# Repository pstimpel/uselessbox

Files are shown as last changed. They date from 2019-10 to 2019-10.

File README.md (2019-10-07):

# uselessbox
Just another useless box

3D printed useless box or so called useless machines. Arduino driven. Features 4 servos and a gesture/proximity sensor. Contains a 16 LED neopixel ring. All parts are easy to source. 

## Video in Action
https://www.youtube.com/watch?v=pDcApzEbbxg

## List of parts, sources (no affiliate links)
1x Arduino Nano V3 5V

1x Gesture/proximity sensor, 5V (!) similar to https://www.distrelec.de/de/naeherungs-licht-rgb-und-gestensensor-apds9960-5v-adafruit-3595/p/30139163

1x switch, similar to https://www.amazon.de/gp/product/B07MY2WVQ3/

1x jack similar to https://www.amazon.de/gp/product/B009PH1J5Y/

1x power adaptor similar to https://www.amazon.de/gp/product/B07HSPT57Y

4x servo motors, similar to https://www.amazon.de/gp/product/B06XQD18QN

cables, solder stuff

22x M3*10 scews

5x M3*8 screws

2x M3*20 screws

1x Neopixel 16 LED ring similar to https://www.distrelec.de/de/neopixel-ring-mit-16-rgb-leds-adafruit-1463-neopixel/p/30091142

1x resistor 1/4W 260 Ohm

1x resistor 1/4W 10 kOhm

20x 2.54mm pin headers

2x 5mm 2pol screw terminals

some steering servo push wire, 0.6mm will do. You need about 10 cm.

some double sided tape

optional: stuff to create PCBs

## Instructions
Optional: create your PCB

Just 3d print the parts, each part one time. I printed the "OK fingers" in 0.1mm, and all other stuff in 0.25mm. I used cubic infill, 2 shells, and 3 shells on bottom and top. I did not use any support except for the LED housing. I was using PLA from https://dasfilament.de

Mount one servo to the back part. The axis on top is showing to the outside. Add the lid servo arm. Mount the lid to the back using M3*20 screws. Now use the steering servo push wire. Make sure your servo is at center position when doing that. Make the wire as long as you need it so the lid and back are located rectangular.

Mount the back to the bottom, using 4 M3*10 screws. 

Mount the usb door using the usb door frame, to the the front. Mount the front to the bottom using 4 M3*10 screws.

Mount the jack to the bottom rear and lock it using the "Buchsenhalter" (sorry, forgot to translate it) to the bottom. Use 2 M3*8 screws.

Solder 5 cables to the gesture sensor board, but do not use the pins for this breakout board. If you have, use some old servo cable or anything similar that would match to pins at your main board if you use any. If there are no pins, you will have to solder the wires to the main board later. Make the cables around 15cm long. Mount the sensor board to the top, using the Sensorlock and 2 M3*8 screws.

Solder 2 cables to your switch. Mount the switch to the top. The "on position" of the switch has to show away from the sensor board. Make these cables around 15cm long.

Solder 3 more cables to your neopixel ring (ground, V+, data in). Make these cables 15 cm long, and use again some old servo cables or other cables matching pins. Add the neopixel ring to the housing, and close it using the LED cover. Btw, print this in transparent filament, if you have. Nice light effects are waiting for you. Lock the housing and the cover by another M3*8 screw. The neopixel ring points towards the cover with its LEDs. Mount the LED housing on top of your top part, and lock it using some M3*10 screws. The LED point towards the front. Moint the "flag arm" to one servo, and this servo to the top part. If you look from behind, the axis points to you and to the left. You can add some white label to the flag holder, to create a small flag. Mount the top to the front using another 4 M3*10 screws.

Mount the finger to one servo, do not lock it up yet. Mount the servo to the right housing part, axis to the right. Mount the right housing to the already mounted parts, mount it on the right side when you look from behind! Use 5 M3*10 screws.

OK, we enter the finish line, slowly...

Mount the 4th servo to the "left" part. Axis point to the front, but downwards. Connect OK fingers and "assholearm" together using another M3*10 screw. Mount the whole arm to the servo. DO NOT CLOSE THE HOUSING YET!

Connect all wires (servos, LED, switch, jack, gesture sensor) to your PCB. Take care for not short cutting anything. Use double sided tape and mount your PCB in a way you can reach the USB of te arduino throught the "usb door" at the front of your housing. Make sure again you do not block any servo movement by cables.

It is time to connect the power adaptor. If nothing smokes, you got your solder job the right way.

Make sure the switch on top of your new toy is in Off position, pointing to the front. Connect USB and your PC. Fire up your Arduino IDE, load the sketch and push it to the Arduino. Maybe you need to activate libraries for servos, or FastLED or the gesture sensor. Just follow the instruction of these vendors.

After the reboot, the LED should light up in blue and kind of glow...if you put your finger on the sensor, it should glow red, brightness depending on how close your finger is to the sensor.

At the same time, all your servos were "reset". You can now tighten all the screws of the servo arms connecting to the servo heads.

Servo for Lid: in reset position the LID should be closed

Servo for Flag: in reset position the flag arm should be horizontal, but below the edge of the top.

Servo for OKFinger/Asshole: The door should be closed, the fingers hidden.

Servo for Finger: Tricky one. Push the switch backwards and watch your finger if it makes it way to the switch. Idealy, it should turn the switch off. Just adjust until this happens. Hint: give a little extra push, just about 2-3 mm. Finally, tighten the screw.

OK, if all mechanics are working as expected, your useless machine should work as expected. You can now close the housing, using the last 5 M3*10 screws.

## What does it do?
Basically, the Arduino will cycle trough different ways the servos work. To start the machine, just push the switch to on. The main task of this machine is to push the switch into its off position.

Step 1: open lid, push switch off

Step 2: open lid very harsh, push switch off. After that the lid will open depending on how close your finger is to the sensor.

Step 3: open lid again, push switch off

Step 4: open lid, waving white flag, close the lid. Open the lid, push off the switch, close the lid.

Step 5: show the OK finger / asshole finger (as you prefer), then open the lid, push the switch, close the lid.

Of course you are invited to extent the possible action, color codes and so on. Just make sure to not use "delay()" too heavy, since this will interrupt the glowing of the LED.

## Frequently asked questions
### Why do you enable and disable the servos that much?
I found my servos to be really cheap ones. They interfere with each other. Disabling the servos I do not need for the moment solved this. However, in the video you can see the servos "choking". If you can, buy quality servos.

## Credits
The "OK finger" was remixed out of https://www.thingiverse.com/thing:3370059 by tdkahn1978 .

## Crosslinks

Repo
https://github.com/pstimpel/uselessbox

Thingiverse
https://www.thingiverse.com/thing:3901482

Prusaprinters
https://www.prusaprinters.org/prints/6042-another-useless-box

Youtube
https://www.youtube.com/watch?v=pDcApzEbbxg

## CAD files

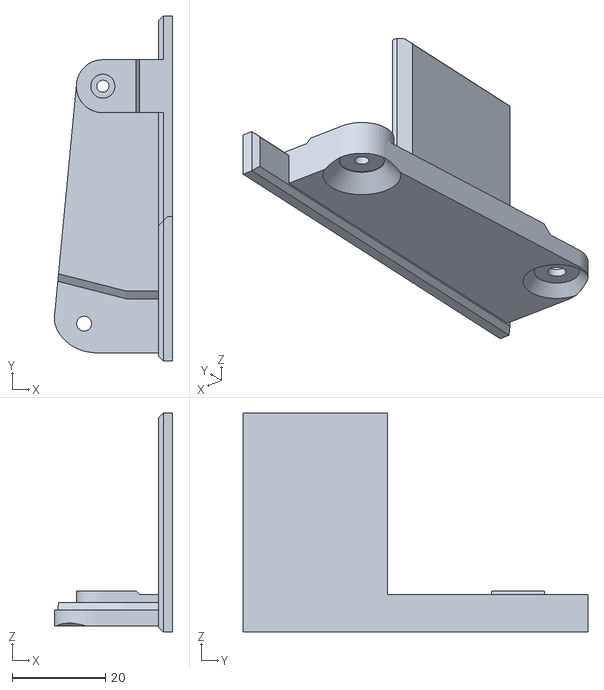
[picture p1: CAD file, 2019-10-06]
stl/AssholeArmv5.stl
25.4 x 74.0 x 47.0

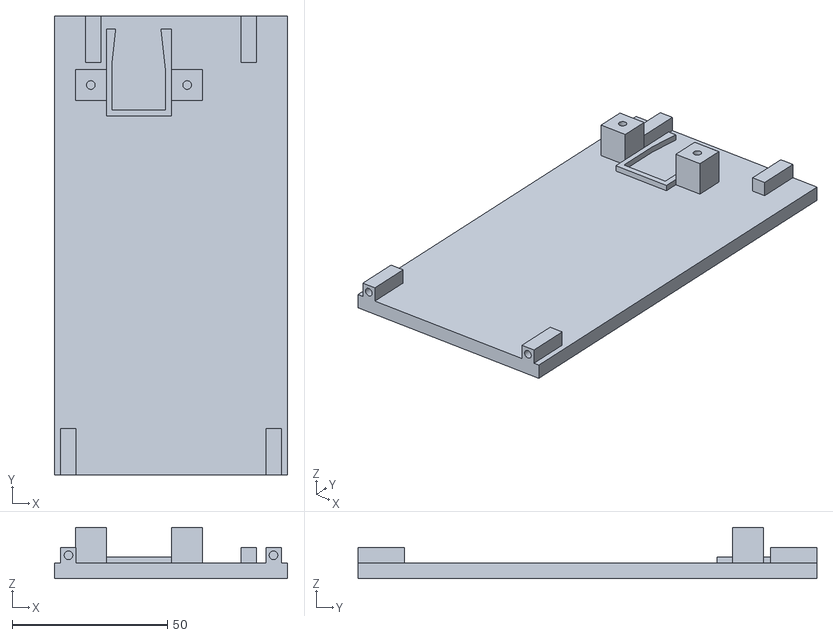
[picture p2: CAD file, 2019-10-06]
stl/BottomV2.stl
75.0 x 147.7 x 16.5

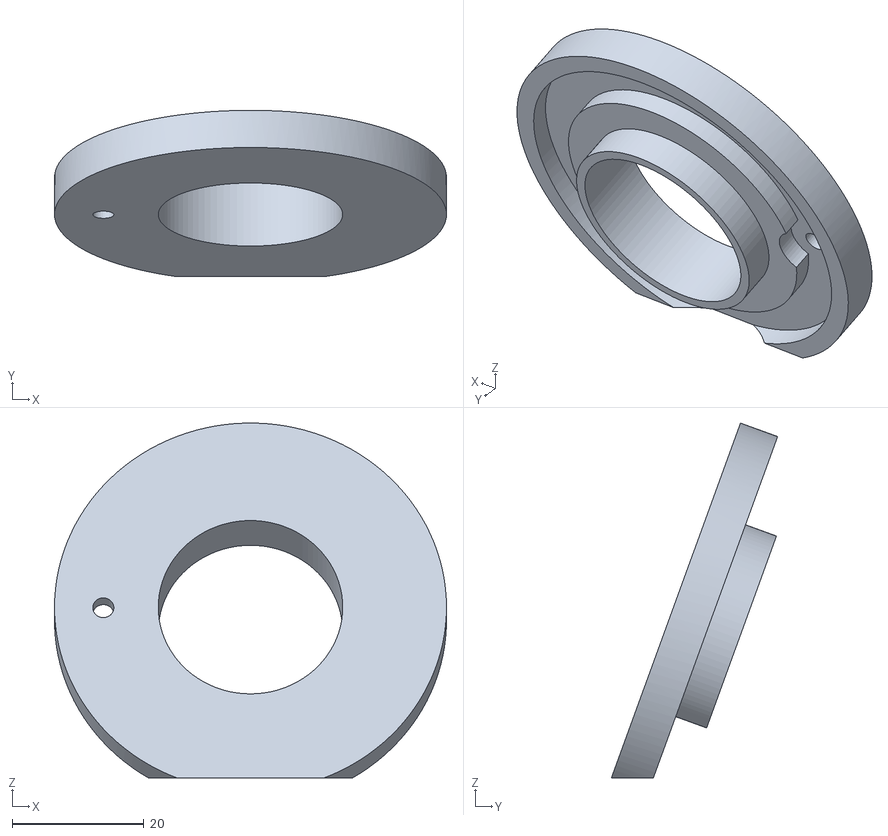
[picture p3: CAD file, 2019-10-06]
stl/LEDCoverv4.stl
59.5 x 25.2 x 53.9

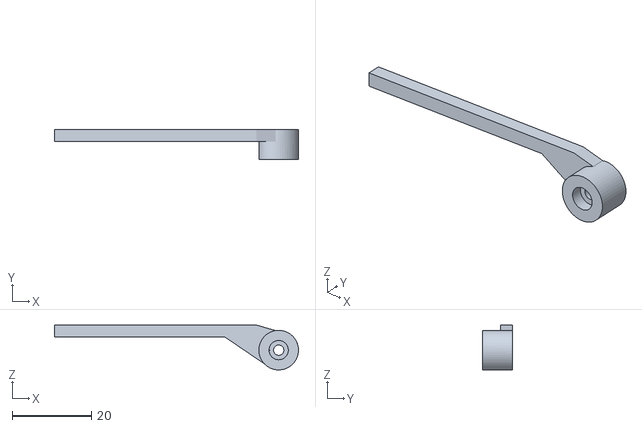
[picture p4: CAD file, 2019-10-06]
stl/WhiteFlagv5.stl
61.6 x 7.50 x 11.3

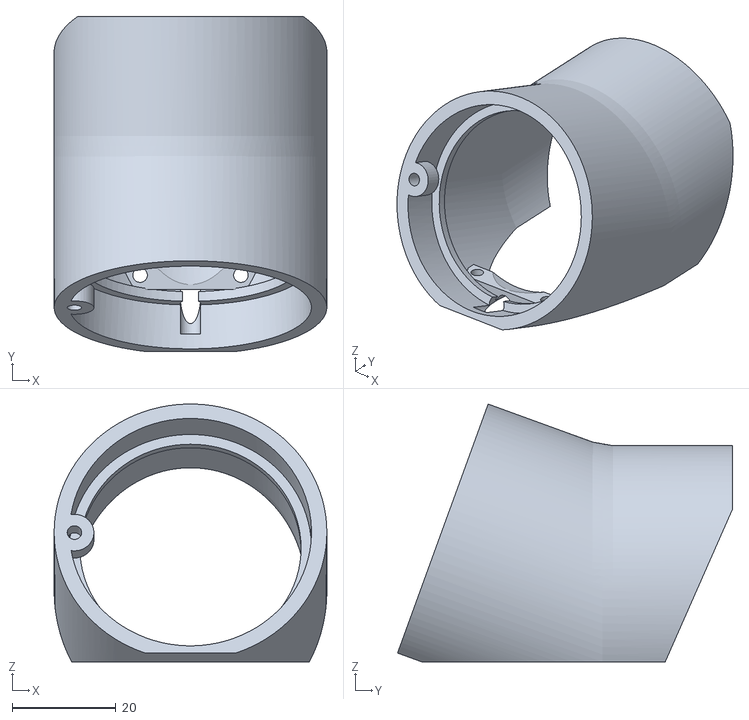
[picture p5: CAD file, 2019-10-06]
stl/LEDhousingv10.stl
52.5 x 64.5 x 49.6

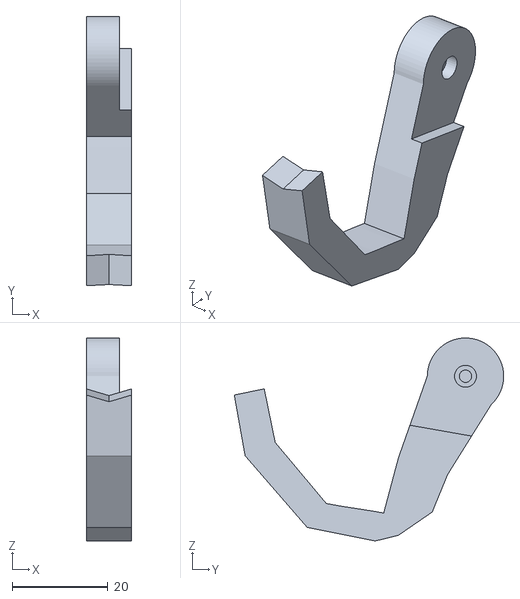
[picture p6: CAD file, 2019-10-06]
stl/Fingerv8.stl
9.50 x 56.4 x 42.5

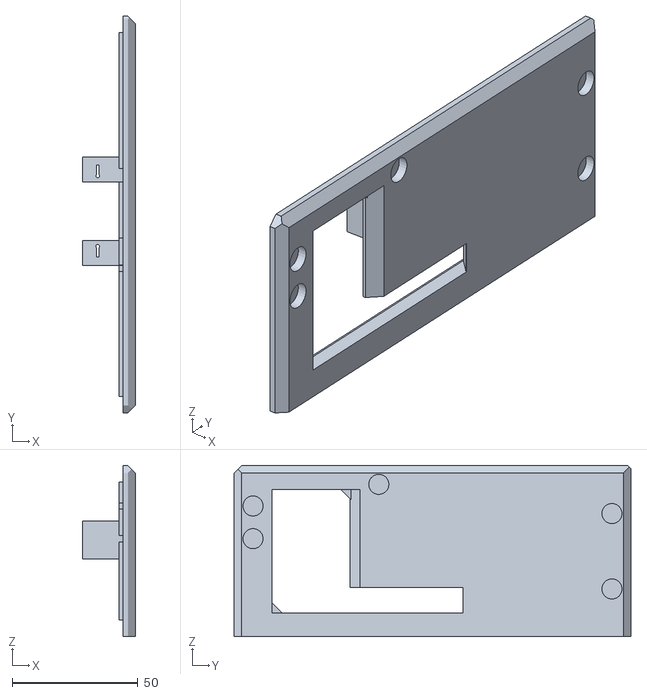
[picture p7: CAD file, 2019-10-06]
stl/Leftv5.stl
21.0 x 157.7 x 68.0

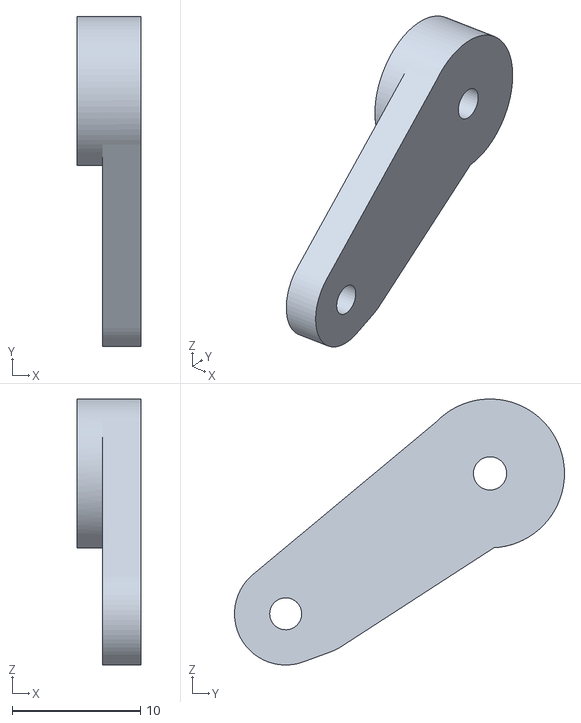
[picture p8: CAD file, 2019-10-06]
stl/LidServoArmv4.stl
5.00 x 25.8 x 20.8

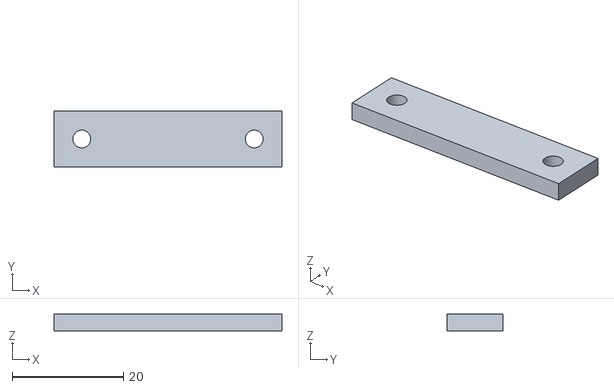
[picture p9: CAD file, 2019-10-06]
stl/BuchsenhalterV2.stl
41.0 x 10.0 x 3.00

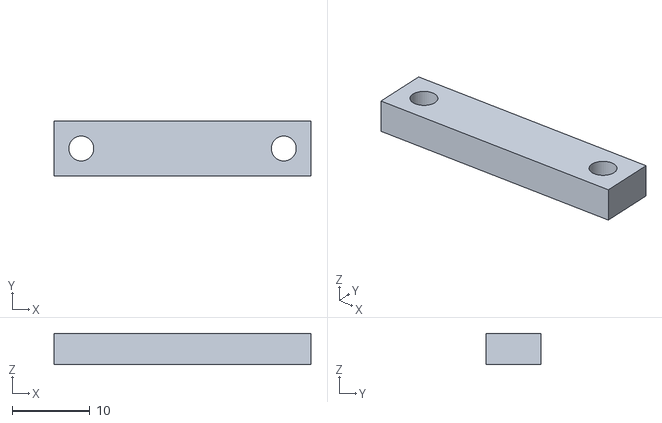
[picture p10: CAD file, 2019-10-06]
stl/SensorLockV2.stl
33.0 x 7.00 x 4.00

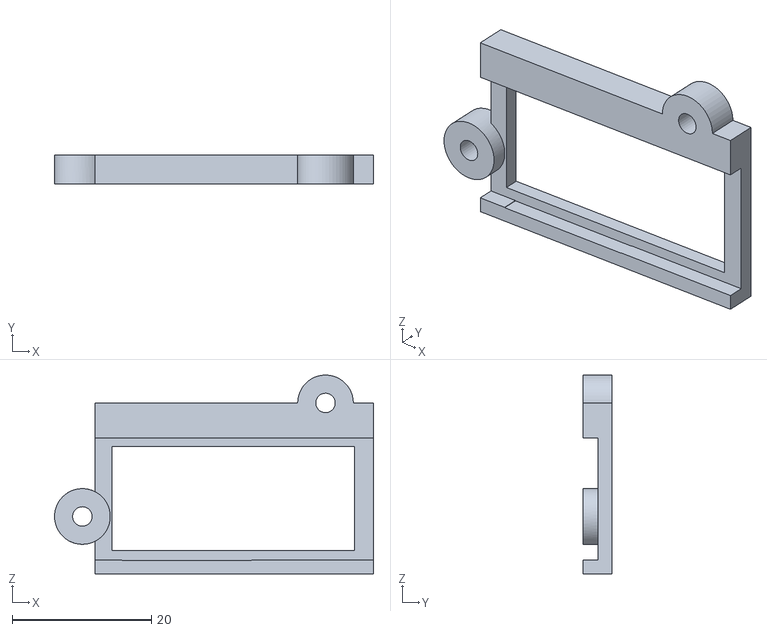
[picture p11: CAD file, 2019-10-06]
stl/USBDoorFrameV2.stl
45.8 x 4.20 x 28.6

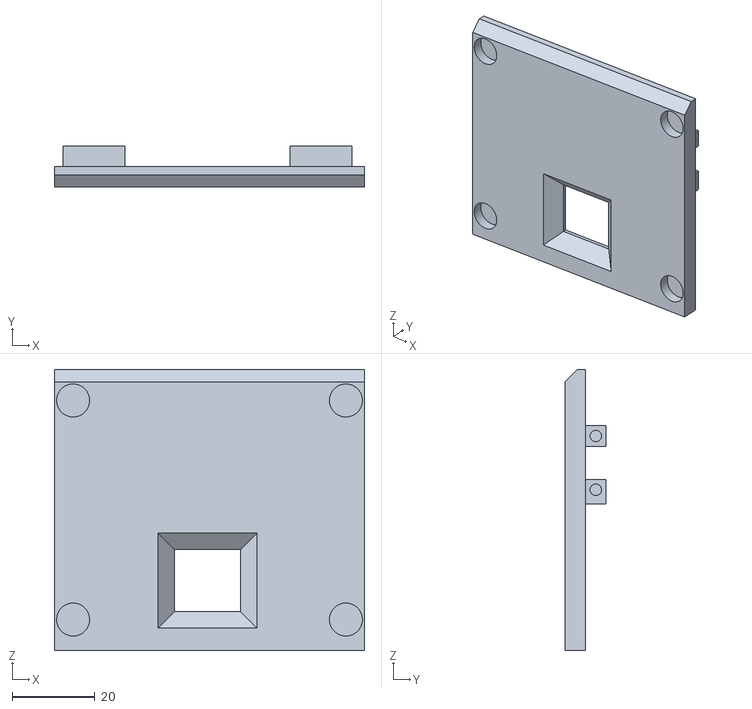
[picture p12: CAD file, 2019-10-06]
stl/FrontV2.stl
75.0 x 10.0 x 68.0

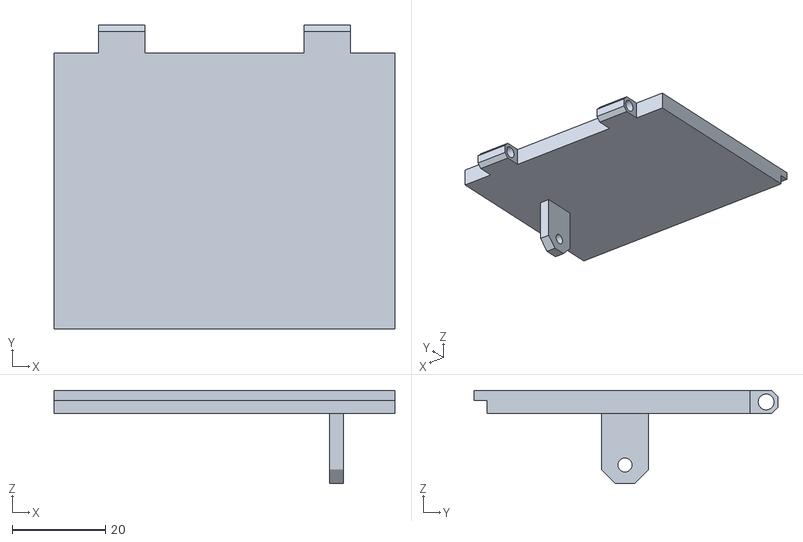
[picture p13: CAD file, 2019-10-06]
stl/LidV2.stl
73.0 x 65.0 x 20.0

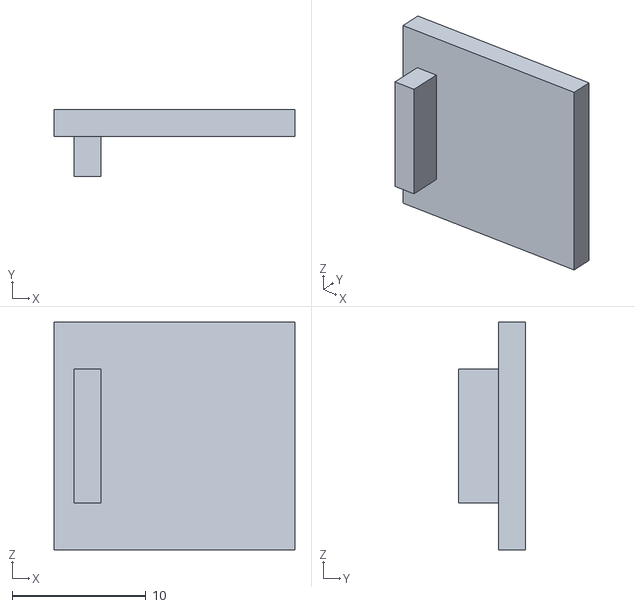
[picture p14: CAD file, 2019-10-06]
stl/USBDoorV2.stl
18.0 x 5.00 x 17.0

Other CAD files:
stl/Backv4.stl
stl/Topv5.stl
stl/RightV4.stl
stl/OKFinger v2.stl

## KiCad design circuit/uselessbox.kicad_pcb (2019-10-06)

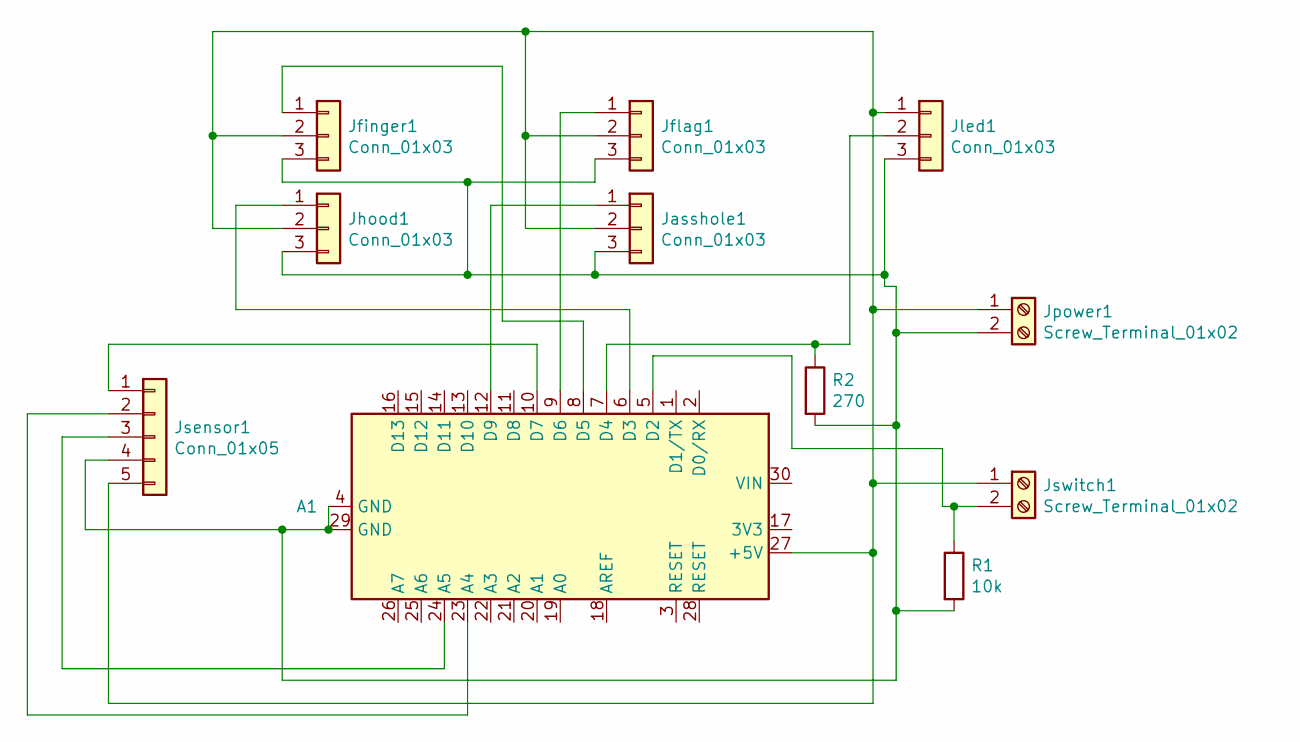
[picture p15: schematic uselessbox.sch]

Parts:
A1: n; Arduino_Nano
Jasshole1: Conn_01x03; PinHeader_1x03_P2.54mm_Vertical
Jfinger1: Conn_01x03; PinHeader_1x03_P2.54mm_Vertical
Jflag1: Conn_01x03; PinHeader_1x03_P2.54mm_Vertical
Jhood1: Conn_01x03; PinHeader_1x03_P2.54mm_Vertical
Jled1: Conn_01x03; PinHeader_1x03_P2.54mm_Vertical
Jpower1: Screw_Terminal_01x02; TerminalBlock_Altech_AK300-2_P5.00mm
Jsensor1: Conn_01x05; PinHeader_1x05_P2.54mm_Vertical
Jswitch1: Screw_Terminal_01x02; TerminalBlock_Altech_AK300-2_P5.00mm
R1: 10k; R_Axial_DIN0204_L3.6mm_D1.6mm_P7.62mm_Horizontal
R2: 270; R_Axial_DIN0204_L3.6mm_D1.6mm_P7.62mm_Horizontal

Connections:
unnamed: A1.5 (D2), Jswitch1.2, R1.1
unnamed: A1.6 (D3), Jhood1.1
unnamed: A1.7 (D4), Jled1.2, R2.1
unnamed: A1.8 (D5), Jfinger1.1
unnamed: A1.9 (D6), Jflag1.1
unnamed: A1.10 (D7), Jsensor1.1
unnamed: A1.12 (D9), Jasshole1.1
unnamed: A1.23 (A4), Jsensor1.2
unnamed: A1.24 (A5), Jsensor1.3
unnamed: A1.27 (+5V), Jasshole1.2, Jfinger1.2, Jflag1.2, Jhood1.2, Jled1.1, Jpower1.1, Jsensor1.5, Jswitch1.1
unnamed: A1.4 (GND), A1.29 (GND), Jasshole1.3, Jfinger1.3, Jflag1.3, Jhood1.3, Jled1.3, Jpower1.2, Jsensor1.4, R1.2, R2.2

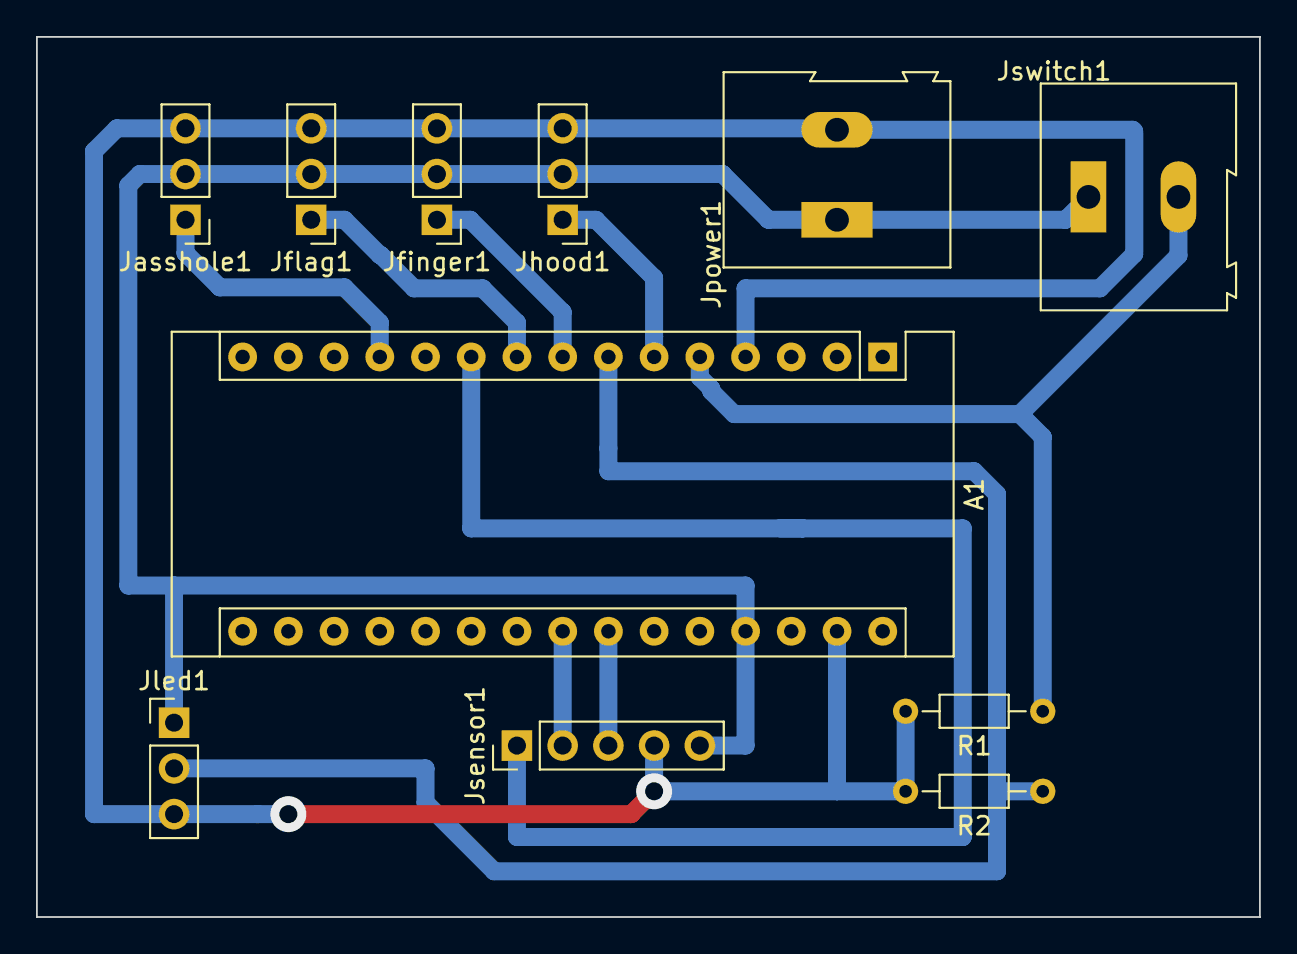
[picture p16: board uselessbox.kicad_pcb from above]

Board: 2 copper layers, 67.9 x 48.9 mm, 11 parts (0 on the bottom side), 11 nets.

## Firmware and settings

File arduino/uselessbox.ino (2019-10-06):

#include <FastLED.h>
#include <Servo.h>
#include "Adafruit_APDS9960.h"
Adafruit_APDS9960 apds;


FASTLED_USING_NAMESPACE

Servo hood, finger, flag, asshole;

#if defined(FASTLED_VERSION) && (FASTLED_VERSION < 3001000)
#warning "Requires FastLED 3.1 or later; check github for latest code."
#endif

#define INT_PIN 7

#define DATA_PIN    4
//#define CLK_PIN   4
#define LED_TYPE    WS2811
#define COLOR_ORDER GRB
#define NUM_LEDS    16
CRGB leds[NUM_LEDS];
CRGBPalette16 gPal;
volatile bool glowstate = false;
volatile int brightness = 150;
volatile int colorcode =1;
int presetbrightness = 150;

int hoodactivestop = 1000;
int hoodinactivestop = 1650;
volatile int hoodcurrent = 1650;
volatile int hoodspeed = 25;
volatile bool hoodservoactive = false;

int fingeractivestop = 1700;
int fingerinactivestop = 1300;
volatile int fingercurrent = 1300;
volatile int fingerspeed = 250;
volatile bool fingerservoactive = false;

int flagactivestop = 2000;
int flaginactivestop = 1500;
volatile int flagcurrent = 1500;
volatile int flagspeed = 150;
volatile bool flagservoactive = false;

int assholeactivestop = 1000;
int assholeinactivestop = 1700;
volatile int assholecurrent = 1700;
volatile int assholespeed = 50;
volatile bool assholeservoactive = false;

volatile bool servoactive = false;
volatile bool servoactionfinished = false;

volatile int currentstep=0;
volatile bool currentstepfinished=false;

volatile bool skipflag = false;
volatile bool skipasshole = false;

#define FRAMES_PER_SECOND  120

volatile bool triggerInUse=false;
volatile bool triggerinprogress = false;

volatile int localloop =-1;

int lowerproximitythreshold=15;

int servopinhood = 3;
int servopinfinger = 5;
int servopinflag = 6;
int servopinasshole = 9;

int pinswitch = 2;
volatile int oldhoodcurrent=0;

void setup() {
  Serial.begin(9600); //init debug console 
  pinMode(INT_PIN, INPUT_PULLUP);
  delay(500); // 500 milliseconds delay for recovery
  pinMode(3, INPUT); //modeswitch
  FastLED.addLeds<LED_TYPE,DATA_PIN,COLOR_ORDER>(leds, NUM_LEDS).setCorrection(TypicalLEDStrip);
  FastLED.setBrightness(brightness);
  if(!apds.begin()){
    Serial.println("failed to initialize device! Please check your wiring.");
  }
  else Serial.println("Device initialized!");

  apds.enableProximity(true);
  apds.setProximityInterruptThreshold(0, lowerproximitythreshold);
  apds.enableProximityInterrupt();
  
  setled(CRGB::White);
  //delay(5000);
  hoodcurrent = hoodinactivestop;
  movehood(hoodcurrent);
  fingercurrent = fingerinactivestop;
  movefinger(fingercurrent);
  flagcurrent = flaginactivestop;
  moveflag(flagcurrent);
  assholecurrent = assholeinactivestop;
  moveasshole(assholecurrent);
  
  enableServos();
  delay(500);  
  servoactive = true;
  executeServo();
  delay(500);
  disableServos();
  delay(500);
  servoactive = false;
  servoactionfinished = true;
  
  setled(CRGB::Black);
  brightness=10;
  
}



void loop()
{

  
  if(!digitalRead(INT_PIN)){
    setled(CRGB::DarkRed);
    int proximity = apds.readProximity();
    //Serial.println(proximity);
    FastLED.setBrightness(proximity);
    //clear the interrupt
    apds.clearInterrupt();
    if(localloop==1) {
      if(hoodservoactive==false) {
        enableServoHood();
        delay(100);
        oldhoodcurrent = hoodcurrent;
      }
      hoodcurrent = map(proximity, lowerproximitythreshold, 255, hoodinactivestop, hoodactivestop);
      if(hoodcurrent > (oldhoodcurrent + 50) || hoodcurrent < (oldhoodcurrent - 50)) {
        oldhoodcurrent=hoodcurrent;
        movehood(hoodcurrent);
        //Serial.println(hoodcurrent);
      }
      if(hoodservoactive==true) {
        disableServoHood();
      }
    }
    
  } else {
    
    FastLED.setBrightness(brightness);
    glow();
  }
  FastLED.show();  
  FastLED.delay(1000/FRAMES_PER_SECOND); 
  
  if(digitalRead(pinswitch) == HIGH) {
    if(triggerInUse==false && triggerinprogress==false) {  
      triggerinprogress=true;
      brightness=presetbrightness;
      FastLED.setBrightness(brightness);
      //Serial.println("------------>trigger");  
      localloop++;
      if (localloop > 5) {
        localloop = 0;
      }
      switch (localloop) {
        case 0: //standard
          skipflag = true;
          skipasshole = true;
          hoodspeed = 25;
          fingerspeed = 250;
          flagspeed = 50;
          assholespeed = 50;
          colorcode=2;
        break;
        case 1: //fast and resolute
          skipflag = true;
          skipasshole = true;
          hoodspeed = 200;
          fingerspeed = 250;
          flagspeed = 250;
          assholespeed = 50;
          colorcode=5;
        break;
        case 2: //open hood based on proximity
          skipflag = true;
          skipasshole = true;
          hoodspeed = 25;
          fingerspeed = 250;
          flagspeed = 150;
          assholespeed = 50;
          colorcode=3;
        break;
        case 3: //wave flag
          skipflag = false;
          skipasshole = true;
          hoodspeed = 25;
          fingerspeed = 250;
          flagspeed = 150;
          assholespeed = 50;
          colorcode=3;
        break;
        case 4: //really slow
          skipflag = true;
          skipasshole = true;
          hoodspeed = 10;
          fingerspeed = 250;
          flagspeed = 150;
          assholespeed = 50;
          colorcode=2;
        break;
        case 5: //show asshole
          skipflag = true;
          skipasshole = false;
          hoodspeed = 25;
          fingerspeed = 250;
          flagspeed = 150;
          assholespeed = 50;
          colorcode=4;
        break;
        default:
          skipflag = true;
          skipasshole = true;
          hoodspeed = 25;
          fingerspeed = 250;
          flagspeed = 150;
          assholespeed = 50;
          colorcode=2;
        break;
      }
      //Serial.print("loop:");
      //Serial.println(localloop);
      servoactive=true;
      servoactionfinished=false;
      currentstep=1;
      currentstepfinished=false;

      //enableServos();

      setled(CRGB::White);
      FastLED.show();
      delay(250);
      

      
      
    } else {
      //Serial.println("----------Trigger in use already");
    }
      
  } else {
    if(triggerInUse==true) {
      brightness=presetbrightness;
      FastLED.setBrightness(brightness);
      //Serial.println("------------>trigger release");  
      setled(CRGB::Black);
      triggerInUse=false;
      triggerinprogress=false;
    }
  }
  
  if(servoactionfinished==true) {
    colorcode=1;
    if(servoactive==true) {
      //disableServos();
      servoactive=false;
      currentstep=0;
    }
    servoactive = false;
    triggerInUse=false;
    triggerinprogress=false;
    
  }
  
  if(servoactive==true && servoactionfinished==false) {

    
    
    //do math staff and so on
    if(currentstepfinished==true && currentstep==9) {
      servoactionfinished=true;
      if(hoodservoactive==true) {
        disableServoHood();
      }
    }
    
    if(currentstepfinished==false && currentstep==8) {
      if(fingerservoactive==true) {
        disableServoFinger();
      }
      if(hoodservoactive==false) {
        enableServoHood();
      }
      if(hoodcurrent < hoodinactivestop) {
        if(hoodcurrent <= (hoodinactivestop - hoodspeed)) {
          hoodcurrent=hoodcurrent+(hoodspeed-1);
          //Serial.println("close hood");
        } else {
          hoodcurrent=hoodinactivestop;
          currentstepfinished=true;
          currentstep++;
          //Serial.println("closed hood");
        }
      }
    }

    if(currentstepfinished==false && currentstep==7) {
      if(fingercurrent > fingerinactivestop) {
        if(fingercurrent >= (fingerinactivestop + fingerspeed)) {
          fingercurrent=fingercurrent-(fingerspeed-1);
          //Serial.println("close finger");
        } else {
          fingercurrent=fingerinactivestop;
          currentstepfinished=false;
          currentstep++;
          //Serial.println("closed finger");
        }
      }
    }

    if(currentstepfinished==false && currentstep==6) {
      if(fingerservoactive==false) {
        enableServoFinger();
      }
      if(flagservoactive==true) {
        disableServoFlag();
      }
      if(fingercurrent < fingeractivestop) {
        if(fingercurrent <= (fingeractivestop - fingerspeed)) {
          fingercurrent=fingercurrent+(fingerspeed-1);
          //Serial.println("raise finger");
        } else {
          fingercurrent=fingeractivestop;
          currentstepfinished=false;
          currentstep++;
          //Serial.println("stay finger");
        }
      }
    }

        
    if(currentstepfinished==false && currentstep==5) {
      
      if(skipflag == true) {
        currentstep++;
      } else {
        if(flagcurrent > flaginactivestop) {
          if(flagcurrent >= (flaginactivestop + flagspeed)) {
            flagcurrent=flagcurrent-(flagspeed-1);
            //Serial.println("close flag");
          } else {
            flagcurrent=flaginactivestop;
            currentstepfinished=false;
            currentstep++;
            //Serial.println("closed flag");
          }
        }
        
      }
    }
    
    if(currentstepfinished==false && currentstep==4) {
      if(hoodservoactive==true) {
        disableServoHood();
      }
      if(skipflag == true) {
        currentstep++;
      } else {
        if(flagservoactive==false) {
          enableServoFlag();
        }
        if(flagcurrent < flagactivestop) {
          if(flagcurrent <= (flagactivestop - flagspeed)) {
            flagcurrent=flagcurrent+(flagspeed - 1);
            //Serial.println("raise flag");
          } else {
            flagcurrent=flagactivestop;
            currentstepfinished=false;
            currentstep++;
            //Serial.println("stay flag");
            //waving the flag
            moveflag(flagcurrent);
            delay(200);
            flagcurrent = flagcurrent-50;
            moveflag(flagcurrent);
            delay(200);
            flagcurrent = flagcurrent-50;
            moveflag(flagcurrent);
            delay(200);
            flagcurrent = flagcurrent+50;
            moveflag(flagcurrent);
            delay(200);
            flagcurrent = flagcurrent+50;
            moveflag(flagcurrent);
            delay(200);
            flagcurrent = flagcurrent-50;
            moveflag(flagcurrent);
            delay(200);
            flagcurrent = flagcurrent-50;
            moveflag(flagcurrent);
            delay(200);
            flagcurrent = flagcurrent+50;
            moveflag(flagcurrent);
            delay(200);
            flagcurrent = flagcurrent+50;
            moveflag(flagcurrent);
            delay(200);
            flagcurrent = flagactivestop;
            
          }
        }
      }
    }
  
    if(currentstepfinished==false && currentstep==3) {
      if(assholeservoactive==true) {
        disableServoAsshole();
      }
      if(hoodservoactive==false) {
        enableServoHood();
      }
      if(hoodcurrent > hoodactivestop) {
        if(hoodcurrent >= (hoodactivestop + hoodspeed)) {
          hoodcurrent=hoodcurrent-(hoodspeed - 1);
          //Serial.println("raise hood");
        } else {
          hoodcurrent=hoodactivestop;
          currentstepfinished=false;
          currentstep++;
          //Serial.println("stay hood");
        }
      }
    }

    if(currentstepfinished==false && currentstep==2) {
      
      if(skipasshole == true) {
        currentstep++;
      } else {
        if(assholecurrent < assholeinactivestop) {
          if(assholecurrent <= (assholeinactivestop - assholespeed)) {
            assholecurrent=assholecurrent+(assholespeed-1);
            //Serial.println("close asshole");
          } else {
            assholecurrent=assholeinactivestop;
            currentstepfinished=false;
            currentstep++;
            //Serial.println("closed asshole");
          }
        }
        
      }
    }
    
    if(currentstepfinished==false && currentstep==1) {
     
      if(skipasshole == true) {
        currentstep++;
      } else {
        if(assholeservoactive==false) {
          enableServoAsshole();
        }
        if(assholecurrent > assholeactivestop) {
          if(assholecurrent >= (assholeactivestop + assholespeed)) {
            assholecurrent=assholecurrent-(assholespeed - 1);
            //Serial.println("raise asshole");
          } else {
            assholecurrent=assholeactivestop;
            currentstepfinished=false;
            currentstep++;
            //Serial.println("stay asshole");
            delay(2000);
          }
        }
      }
    }
  

    
    executeServo();
    delay(50);
  }
  
}

void enableServoHood() {
  hood.attach(servopinhood);
  hoodservoactive=true;
}
void enableServoFinger() {
  finger.attach(servopinfinger);
  fingerservoactive=true;
}
void enableServoFlag() {
  flag.attach(servopinflag);
  flagservoactive=true;
}
void enableServoAsshole() {
  asshole.attach(servopinasshole);
  assholeservoactive=true;
}
void disableServoHood() {
  hood.detach();
  hoodservoactive=false;
}
void disableServoFinger() {
  finger.detach();
  fingerservoactive=false;
}
void disableServoFlag() {
  flag.detach();
  flagservoactive=false;
}
void disableServoAsshole() {
  asshole.detach();
  assholeservoactive=false;
}

void enableServos() {
  hood.attach(servopinhood);
  finger.attach(servopinfinger);
  flag.attach(servopinflag);
  asshole.attach(servopinasshole);
  //delay(500);
}

void disableServos() {
  hood.detach();
  finger.detach();
  flag.detach();
  asshole.detach();
  //delay(500);
}

void executeServo() {
  if(servoactive==true) {
    //hood
    movehood(hoodcurrent);
    //Serial.print("hood Servo moved to ");
    //Serial.println(hoodcurrent);
    
    //finger
    movefinger(fingercurrent);
    //Serial.print("finger Servo moved to ");
    //Serial.println(fingercurrent);
    
    //flag
    moveflag(flagcurrent);
    //Serial.print("flag Servo moved to ");
    //Serial.println(flagcurrent);
    
    //asshole
    moveasshole(assholecurrent);
    //Serial.print("asshole Servo moved to ");
    //Serial.println(assholecurrent);
    
  }
}




void movefinger(int speed) {
  int angle = map(speed, 1000, 2000, 0, 180);
  finger.write(angle);
}

void movehood(int speed) {
  int angle = map(speed, 1000, 2000, 0, 180);
  hood.write(angle);
}
void moveflag(int speed) {
  int angle = map(speed, 1000, 2000, 0, 180);
  flag.write(angle);
  
}

void moveasshole(int speed) {
  int angle = map(speed, 1000, 2000, 0, 180);
  asshole.write(angle);
}

void allwhite() {
      setled(CRGB::White);
      FastLED.show();
       
}

void allblack() {
      setled(CRGB::Black);
      FastLED.show();
       
}

void glow() {
      CRGB color;
      switch(colorcode) {
          case 1:
            color = CRGB::DarkBlue;
            break;
          case 2:
            color = CRGB::Yellow;
            break;
          case 5:
            color = CRGB::OrangeRed;
            break;
          case 3:
            color = CRGB::DarkGreen;
            break;
          case 4:
            color = CRGB::Pink;
            break;
          default:
            color = CRGB::DarkRed;    
      }


      setled(color);
      
      if(glowstate==false) {
        if(brightness<presetbrightness) {
          brightness=brightness+3;
          if(brightness>=presetbrightness) {
            glowstate=true;
          }
        } else {
          glowstate=true;
        }
      } else {
        if(brightness>10) {
          brightness=brightness-3;
          if(brightness<=10) {
            glowstate=false;
            colorcode=random(0,3);
            colorcode=1;//keep red
          }
        } else {
          glowstate=false;
        }

      }
      addGlitter(20);
      FastLED.setBrightness(brightness);
      FastLED.show();
      delay(1);
      setled(color);
      FastLED.setBrightness(brightness);
      FastLED.show();
      delay(15);  

      //delay(1000); 
}

void setled(CRGB ledcolor) {
  for( int i = 0; i < NUM_LEDS; i++) {
    leds[i] = ledcolor;
  }
}

void addGlitter( fract8 chanceOfGlitter) 
{
  if( random8() < chanceOfGlitter) {
    leds[ random16(NUM_LEDS) ] += CRGB::White;
  }
}

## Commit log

2019-10-06 Arduino stuff and KICAD project for circuit and pcb
    [uselessbox.kicad_pcb, uselessbox.sch]
2019-10-06 STL files and readme
    [AssholeArmv5.stl, Backv4.stl, BottomV2.stl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]
